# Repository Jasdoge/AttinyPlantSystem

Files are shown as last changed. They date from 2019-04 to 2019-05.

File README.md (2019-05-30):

# Attiny85 Plant Waterer
A project for converting a windshield wiper jug to an automatic plant waterer
Video:

View the making of here (https://www.youtube.com/watch?v=Fqjugu2UjO8)

**Update**: Added an Attiny13 branch which will run on the same hardware (except the MCU obviously).

Circuit and mesh files can be found in the parts directory. The cap I printed was made for the OKQ8 windshield wiper fluid jug. So if you're intending on copying this project, you'll likely want to design your own. I've supplied the 3d models for reference.

Parts used:

| Part | Amount | Where I bought mine |
|---|---|---|
| Empty, washed windshield wiper fluid jug | 1 | Gas station. I use a 4L one by OKQ8. |
| 0.1uF Ceramic capacitor | 1 | Generic component, sold in most component stores |
| 10uF Capacitor | 1 | Generic component, sold in most component stores |
| 100uF+ Capacitor | 1 | Generic component, sold in most component stores |
| LED | 1 | Generic component, sold in most component stores |
| 2-pole plug pairs | 2 | https://www.aliexpress.com/item/10pairs-150mm-JST-male-female-connector-plug-cable-for-RC-ESC-LIPO-Battery-Helicopter-DIY-FPV/32651366625.html |
| Attiny85 | 1 | Sold in a lot of places |
| Attiny85 breakout socket | 1 | https://www.digikey.com/product-detail/en/adam-tech/ICS-308-T/2057-ICS-308-T-ND/9829299 |
| Schottky Diode rated to handle your motor | 1 | https://www.digikey.com/product-detail/en/smc-diode-solutions/11DQ03TR/1655-1893-1-ND/7914877 |
| PCB prototype board | 1 | https://www.digikey.com/product-detail/en/sparkfun-electronics/PRT-08808/1568-1652-ND/7387401 |
| 3pin JST connector pair | 1 | https://www.digikey.com/product-detail/en/jst-sales-america-inc/B3B-XH-A(LF)(SN)/455-2248-ND/1651046 + https://www.digikey.com/product-detail/en/jst-sales-america-inc/03JQ-BT/455-2966-ND/5875089 |
| NPN transistor rated to handle the motor | 1 | Generic component. I used BC337-25 |
| Submersible pump | 1 | https://www.aliexpress.com/item/2018-Brand-New-Micro-Submersible-and-Amphibious-DC-Motor-Pump-Water-pump-3-4-5V-80/32894401053.html |
| Button | 1 | https://www.digikey.com/product-detail/en/e-switch/TL2230EEF100/EG6030-ND/3778181 |
| 2.2kOhm resistor | 1 | Generic component |
| 10kOhm resistor | 1 | Generic component |
| ~100Ohm resistor | 1 | Generic component |
| Tube that fits the motor | 1 | Generic component. Mine was 10mm outer, 8mm inner |
| Moisture sensor | 1 | https://www.aliexpress.com/item/Free-Shipping-Soil-Hygrometer-Humidity-Detection-Module-Moisture-Water-Sensor-Soil-moisture-for-Arduino/32704803481.html |
| 3d-printing parts for the case | 1 | I used PLA for the case and PETG for the pin. |
| Long M3 screws for the case | 1 | Local hardware store |

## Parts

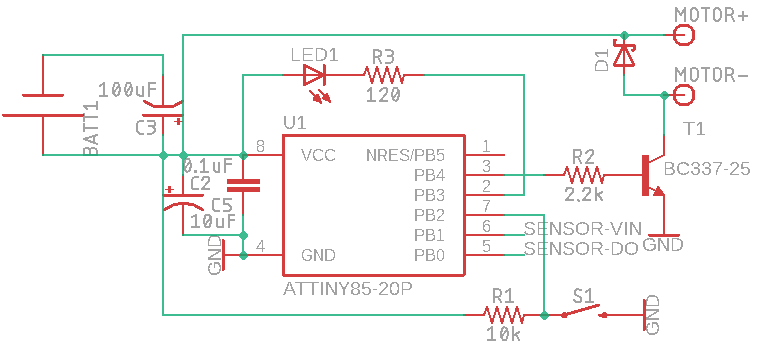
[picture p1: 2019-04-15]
parts/circuit.png

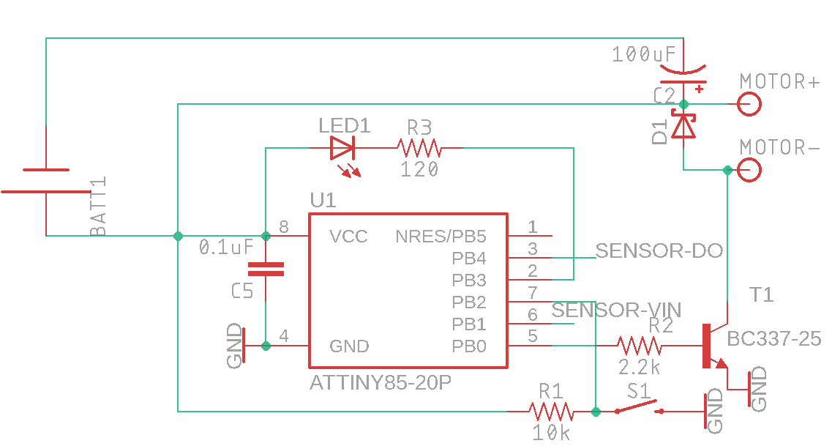
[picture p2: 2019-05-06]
parts/version_2.png

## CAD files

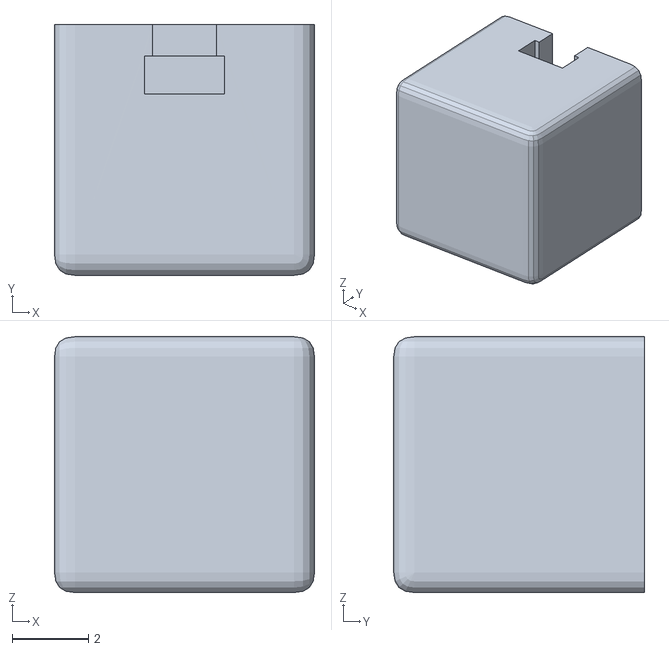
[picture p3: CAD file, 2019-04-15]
parts/switch_button.STL
6.81 x 6.56 x 6.70

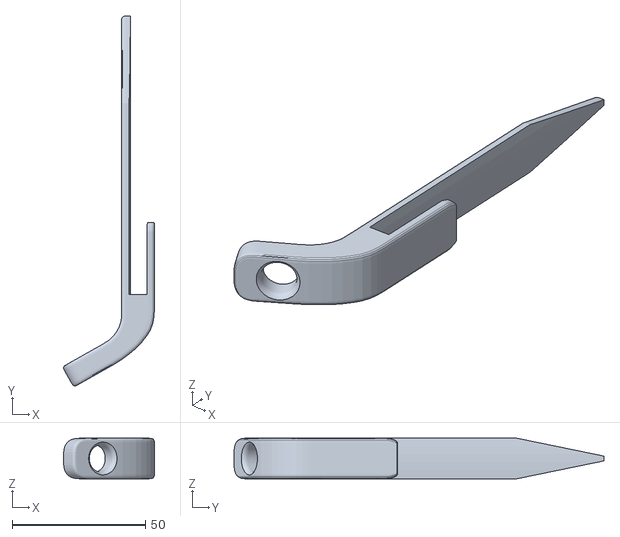
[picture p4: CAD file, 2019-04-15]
parts/vase_pin.STL
34.1 x 138.9 x 15.2

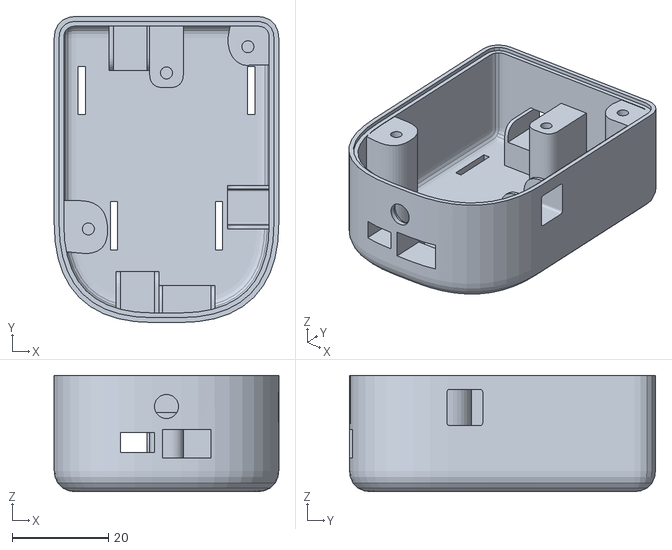
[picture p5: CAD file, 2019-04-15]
parts/enclosure_bottom.STL
46.7 x 63.6 x 24.2

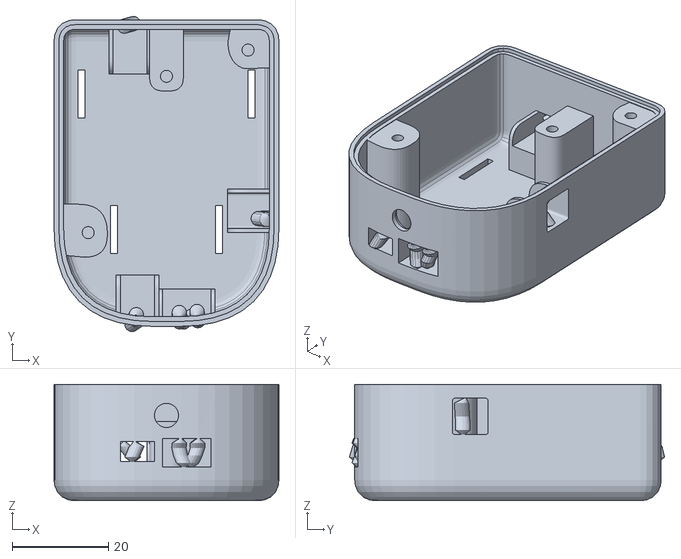
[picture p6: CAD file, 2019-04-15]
parts/enclosure_bottom_tree_supports.stl
46.7 x 65.4 x 24.2

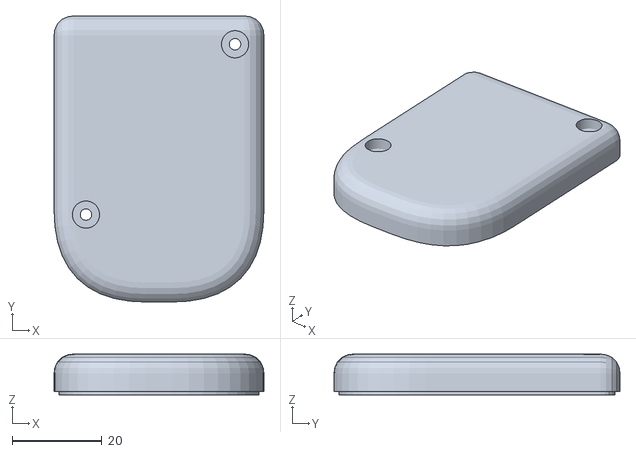
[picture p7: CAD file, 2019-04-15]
parts/enclosure_lid.STL
46.7 x 63.6 x 9.09

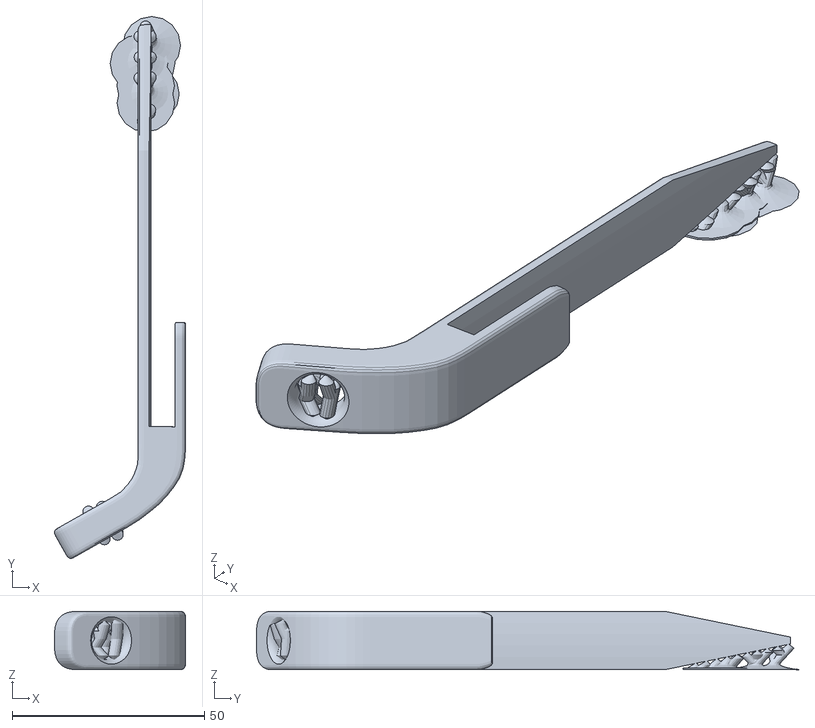
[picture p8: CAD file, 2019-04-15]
parts/vase_pin_tree_supports.stl
34.1 x 141.0 x 15.2

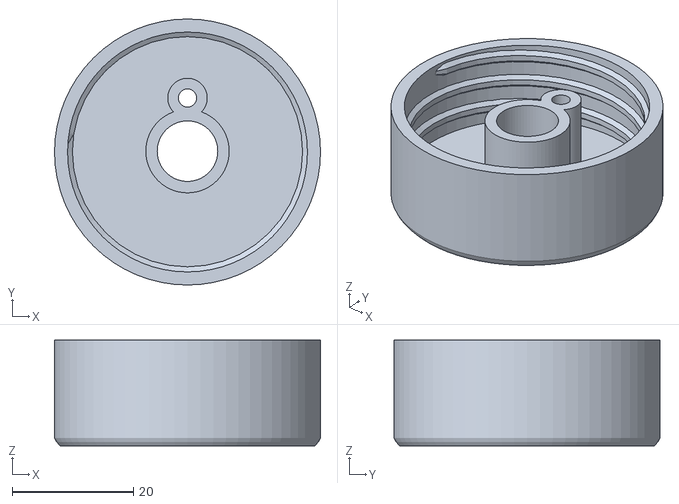
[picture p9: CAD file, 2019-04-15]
parts/bottlecap.STL
44.0 x 44.0 x 17.5

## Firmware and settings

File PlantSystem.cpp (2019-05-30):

#define ATTINY
// #include <Arduino.h>
#include "PlantSystem.h"
#include <avr/sleep.h>
#include <avr/wdt.h>

#define adc_disable() ADCSRA &= ~ bit(ADEN) // disable ADC (before power-off)
#define adc_enable()  (ADCSRA |=  (1<<ADEN)) // re-enable ADC

// Captures wakeup
ISR(WDT_vect) {
	wdt_disable();  // disable watchdog
}

PlantSystem::PlantSystem(){}


void PlantSystem::ini(){

	adc_disable();	// ADC pulls a lot of current, without it, we get down to ~1uA while sleeping
	pinMode(pin_pump, OUTPUT);
	pinMode(pin_sensor_output, OUTPUT);
	pinMode(pin_sensor_input, INPUT);
	pinMode(pin_config_button, INPUT_PULLUP);
	pinMode(pin_debug_led, OUTPUT);
	digitalWrite(pin_pump, LOW);
	digitalWrite(pin_sensor_output, LOW);
	digitalWrite(pin_debug_led, HIGH);		// Connected on cathode
	is_debug_mode = digitalRead(pin_config_button) == LOW;

	byte flashes = is_debug_mode ? 5 : 2;
	digitalWrite(pin_sensor_output, HIGH);
	bool h = true;	// LED lights while LOW, so start at HIGH
	for( byte i=0; i<flashes; ++i ){

		h = !h;
		digitalWrite(pin_debug_led, h);
		delay(250);

	}

}

void PlantSystem::togglePump( bool on ){
	
	
	digitalWrite(pin_debug_led, !on);
	if( on ){
		pump_started = millis();
		// Fade in over ~0.5 sec
		for( byte i=0; i<=255; i=i+5 ){
			analogWrite(pin_pump, i);
			delay(10);
		}
	}
	else{
		pump_started = 0;
		digitalWrite(pin_pump, LOW);
	}
}


void PlantSystem::enableWatchdog(){  
	MCUSR = 0;                          // reset various flags
	WDTCR |= 0b00011000;               // see docs, set WDCE, WDE
	WDTCR =  0b01100001;    			// set WDIE, and 8s delay
	wdt_reset();
	set_sleep_mode (SLEEP_MODE_PWR_DOWN);  
	sleep_mode();            // now goes to Sleep and waits for the interrupt
} 


void PlantSystem::sleep(){

	togglePump(false);

	pinMode(pin_sensor_input, OUTPUT);
	digitalWrite(pin_sensor_input, LOW);
	pinMode(pin_config_button, OUTPUT);
	digitalWrite(pin_config_button, LOW);

	for( int cycles = 0; cycles < num_sleep_cycles; ++cycles )
		enableWatchdog();

	// restart
	ini();

}

void PlantSystem::loop(){

	const long ms = millis();

	if( is_debug_mode ){
		delay(1000);
		return;
	}


	// Stop the pump if started and reached the end of the cycle
	if( pump_started && pump_started+water_duration < ms ){
		togglePump(false);
		// pump finished, sleep again
		sleep();
		return;
	}

	// Pump is not running, take a reading
	if( !pump_started ){

		digitalWrite(pin_sensor_output, HIGH);
		delay(10);
		const bool reading = digitalRead(pin_sensor_input);
		digitalWrite(pin_sensor_output, LOW);

		#ifndef ATTINY
			Serial.printf("Reading: %i\n", reading);
		#endif

		// It's dry, start watering
		if( reading == dry_on )
			togglePump(true);
		// It's not dry, sleep
		else
			sleep();

	}

	
	
}

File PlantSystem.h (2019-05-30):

#ifndef PlantSystem_h
#define PlantSystem_h
#include <Arduino.h>

// Attiny85
#define PIN_PUMP 0
#define PIN_SENSOR_OUTPUT 1
#define PIN_SENSOR_INPUT 4
#define PIN_DEBUG_LED 3
#define PIN_CONFIG_BUTTON 2



class PlantSystem{

	public:
		PlantSystem();
		void ini();
		void loop();
		void togglePump( bool on );
		void sleep();
		void enableWatchdog();
		
		// Configuration
		const byte num_sleep_cycles = 75;			// Sleep cycles at 8sec each. 450 = 1h, 75 = 10 min
		const int water_duration = 10000;			// How long to pump water in ms.	
		bool is_debug_mode = false;

		const uint8_t pin_pump = PIN_PUMP;
		const uint8_t pin_sensor_input = PIN_SENSOR_INPUT;
		const uint8_t pin_sensor_output = PIN_SENSOR_OUTPUT;
		const uint8_t pin_debug_led = PIN_DEBUG_LED;
		const uint8_t pin_config_button = PIN_CONFIG_BUTTON;
	private:
		long pump_started = 0;				// Time when pump was started
		const bool dry_on = HIGH;					// When should the plant be watered?

};

#endif

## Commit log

2019-04-10 Add debug LED and calibration
2019-04-15 Fix debug mode led toggle
    [PlantSystem.cpp, PlantSystem.h]
2019-04-15 Add assets
    [bottlecap.STL, circuit.sch, enclosure_bottom.STL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]
2019-05-06 Version 2. Reduced nr of parts. PWM fade to limit inrush current. Pins 0 and 4 switched Blinks on boot to indicate status
    [circuit.sch, version_2.sch]
2019-05-11 use internal pullup on config
    [version_3.sch]
